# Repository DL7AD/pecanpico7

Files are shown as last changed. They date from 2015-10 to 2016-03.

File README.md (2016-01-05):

# Pecan Pico 7 Balloon Tracker

Pecan Pico 7 is an APRS & SSDV Tracker based on the STM32F429 microcontroller. Please note that this PCB is untested.

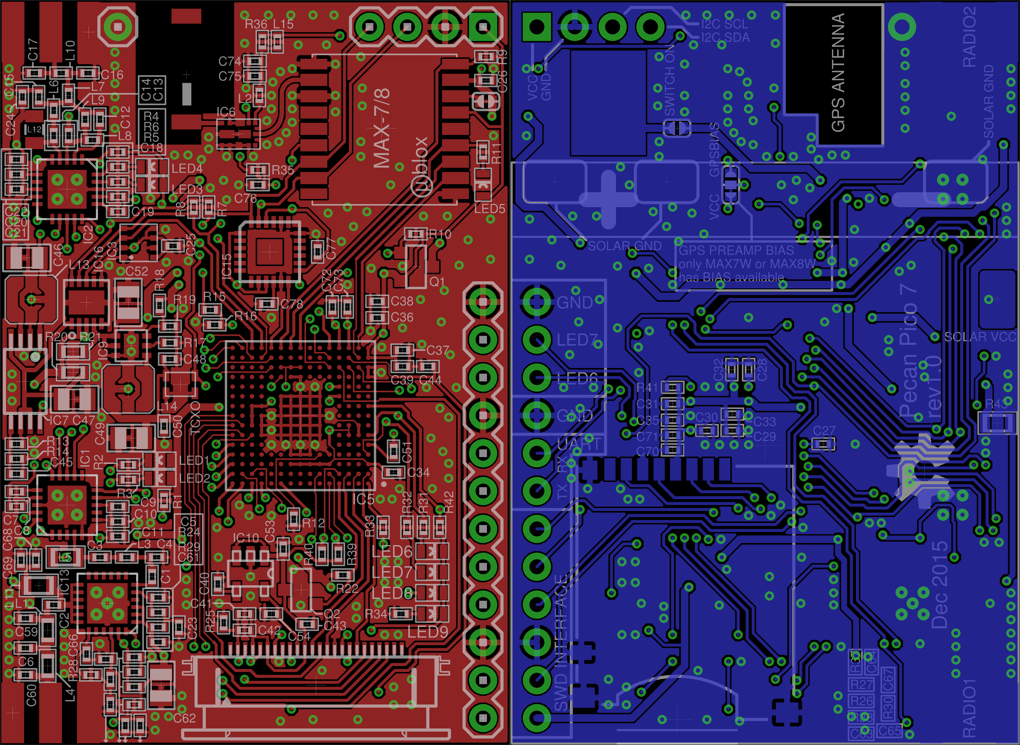
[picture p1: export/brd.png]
Pecan Pico 7


Components
==========

| Component | Description | Purpose on PCB
| --- | --- | ---
| [**Camera OV9655 option**](https://raw.githubusercontent.com/DL7AD/pecanpico7/master/export/sch_camera.png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)
| TI TC1185-1.8VCT713 | LDO | Generate camera core voltage
| OmniVision OV9655 | Camera | Taking pictures
| [**Camera OV2640 option**](https://raw.githubusercontent.com/DL7AD/pecanpico7/master/export/sch_camera.png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)
| TI LP5951MF-1.3/NOPB | LDO | Generate camera core voltage
| OmniVision OV2640 | Camera | Taking pictures
| [**Clock**](https://raw.githubusercontent.com/DL7AD/pecanpico7/master/export/sch_clock.png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)
| Epson TG-5006CJ-19H | TCXO 26MHz | Generate clock for STM32 and transceivers
| [**GNSS**](https://raw.githubusercontent.com/DL7AD/pecanpico7/master/export/sch_gps.png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)
| ublox MAX-7C | GNSS receiver | Receive GPS or GLONASS
| Avago ALM-GP003 | Preamplifier | Filters and preamplifies GNSS signal
| [**IO**](https://raw.githubusercontent.com/DL7AD/pecanpico7/master/export/sch_io.png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)
| *not specified* | microSD card | Flash memory (take any microSD card whatever you want)
| [**Micro Processor Unit (MPU)**](https://raw.githubusercontent.com/DL7AD/pecanpico7/master/export/sch_mpu.png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)
| STM32F429IIH6 | MCU | Controlling all actions on the PCB
| [**Power management**](https://raw.githubusercontent.com/DL7AD/pecanpico7/master/export/sch_power_management.png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)
| ST SPV1040 | Solar battery charger  | Charging the battery from solar cells
| TI TPS62260DRVT | Step-Down regulator | Step down voltage from battery to Vcc rail (2.5V)
| Microchip PAC1720-1-AIA-TR | Current/Voltage sensor | Measure battery input and output current and battery voltage
| [**Radios**](https://raw.githubusercontent.com/DL7AD/pecanpico7/master/export/sch_radios.png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)
| SiLabs Si4060 (Radio 1) | Transmitter (2m) | Transmitting on 2m with 3W
| rfmd RF6886 | Power amplifier | Amplify singal from Radio 1
| SiLabs Si4464 (Radio 2) | Transceiver (70cm) | Transmit and Receive on 70cm with 10mW
| [**Sensing**](https://raw.githubusercontent.com/DL7AD/pecanpico7/master/export/sch_sensing.png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)
| Bosch BME280 | Airpressure sensor | Measuring airpressure, humidity, temperature
| Invensense MPU-9250 | Power amplifier | Measure acceleration, rotation, Earth's magnetic field

Bus connections to peripheral devices
=====================================

There are two I2C bus and one SPI and two UART buses available on the the PCB.
The SPI bus is dedicated to the SiLabs radios. One UART is connected to the GNSS
receiver while the other is available for external debugging purposes. There are
two additional I2C buses. One is used for the camera while the other is used for
everything else. This has been done to avoid routing the I2C through dense
regions on the PCB. The second bus of the I2C can be accessed by a pin header
for external peripheral devices such as an external BME280 to measure balloon
pressure.

**I2C**

| Bus | SCL  | SDA
| --- | ---- | ----
| 1 | PB8  | PB9
| 2 | PB10 | PB11

| Component | Bus | Address
| --- | --- | ---
| OmniVision OV9655/OV2640 | 1 | 0x30
| ublox MAX-7C | 2 | 0x42
| Microchip PAC1720-1-AIA-TR  | 2 | 0x4C
| Bosch BME280 | 2 | 0x77
| Invensense MPU-9250 | 2 | 0x69
| External pin header | 2 | -

**SPI**

- SPI SCK: PB13
- SPI MISO: PB14
- SPI MOSI: PB15

| Component | CS at STM32
| --- | ---
| SiLabs Si4060 (Radio 1) | PA11
| SiLabs Si4464 (Radio 2) | PB0

**UART**

| Component | STM32 TXD | STM32 RXD
| --- | --- | ---
| uBlox MAX-7C | PA2 | PA3
| External pin header | PA0 | PA1

Power feeding
=============

Since this tracker is designed for solar use, there's a solar charging chip, a
battery (LiPo) and a discharging regulator on it. The SPV1040 will charge the battery
on the back of the PCB. It will charge the battery up to 4.1V. The voltage of the
battery is then steped down to 2.5V by the TPS62260 which is fed by the battery. With
exception of the RF6886 All parts are fed by the 2.5V (Vcc) rail. The RF6886 is
connected directly to VBAT in order to get more power out of it. The PAC1720 is able
to measure the charge and discharge current of the battery.

**! PCB ERROR:** The PAC1720 can't measure the current consumed by RF6886.

The camera needs an addional voltage for the core. This must be 1.3V (OV2640) or 1.8V
(OV9655). Depending on which camera is used, IC10 must be changed (notes in schematic).
IC10 is switched by Q2 (GPS shutdown MOSFET). If the camera is switched off, IC10
does not get power as well.

Components Shutdown
===================

Every component has it's own shutdown capacility. Some components are switched off
by an additional MOSFET because when standard shutdown functions still need some mA.

| Component | Shutdown | Notes
| --- | --- | ---
| Microchip PAC1720-1-AIA-TR | none | Standby current 5.5uA
| Radio 1 | Pull PA12 high |
| Radio 2 | Pull PB12 high |
| rfmd RF6886 | none |
| Bosch BME280 | none | Standby current 0.2uA
| MPU-9250 | none | Idle mode 8uA
| Camera | Pull PE0 high  | Camera SHDN still draws 1mA
| Clock (TCXO) | none | Needed for STM32 all time
| GPS and GPS preAMP | Pull PE7 high  |
| microSD card | none | SD cards have usually good internal shutdown
| STM32 | none |

Camera connection
=================

The camera is connected to the DCMI interface of the STM32F4 which can handle the
data though the microcontroller internally. The camera itself is connected to a FFC
connector on the PCB. The STM32 data pins are connected to

| STM32 Pin | Function
| --- | ---
| PA4 | DCMI_HSYNC
| PA6 | DCMI_PCLK
| PB6 | DCMI_D5
| PB7 | DCMI_VSYNC
| PC6 | DCMI_D0
| PC7 | DCMI_D1
| PC8 | DCMI_D2
| PE4 | DCMI_D3
| PB6 | DCMI_D4
| PE5 | DCMI_D6
| PE6 | DCMI_D7

Known PCB errors
================

**ERROR 1:** RF6886 connected incorrectly to PAC1720 (fixable)<br />
Effect: PAC1720 can't measure the current consumed by RF6886<br />
Solution: *none* (will be fixed on next revision)

**ERROR 2:** Capacitor missing at TPS62260DRVT (fixable)<br />
Effect: This capacitor is responsible to reduce voltage ripple on Vcc rail.<br />
Solution: Solder a capacitor (22pF 0402) on top of R18

**ERROR 3:** BYPASS_REG connected to Vcc (fixable)<br />
Effect: The STM32 doesn't starup because internal voltage regulate is shut down<br />
Solution: Desolder R41 and connect BYPASS_REG to GND (put solder junction to resistor pad next to R41)

**ERROR 4:** Wrong oscillator only supplies 0.7V (fixable)<br />
Effect: The external oscillator can't be used for the STM32<br />
Solution: Use an TXC 7L 26MHz oscillator instead or use the internal oscillator

**WARNING 1:** LEDs connected to transceivers are switched on<br />
Effect: Current draw on startup. It could prevent the PCB to startup when the battery is dischanged completely, when the SPV1040 doesn't provide enough power. So the STM32 doesnt boot.<br />
Solution: *none* (will be fixed on next revision) or desolder LEDs

**WARNING 2:** Pad extremly large on PAC1720 and MPU9250<br />
Effect: It could cause solder junctions in production<br />
Solution: *none* (will be fixed on next revision) or put less solder on the pads

**WARNING 3:** Solder jumper included in soldermask<br />
Effect: *no electrical effect*<br />
Solution: *none* (will be fixed on next revision)

**WARNING 4:** RF6886 draws much current in idle<br />
Effect: *no functional limitation*<br />
Solution: *none* (will be fixed on next revision)

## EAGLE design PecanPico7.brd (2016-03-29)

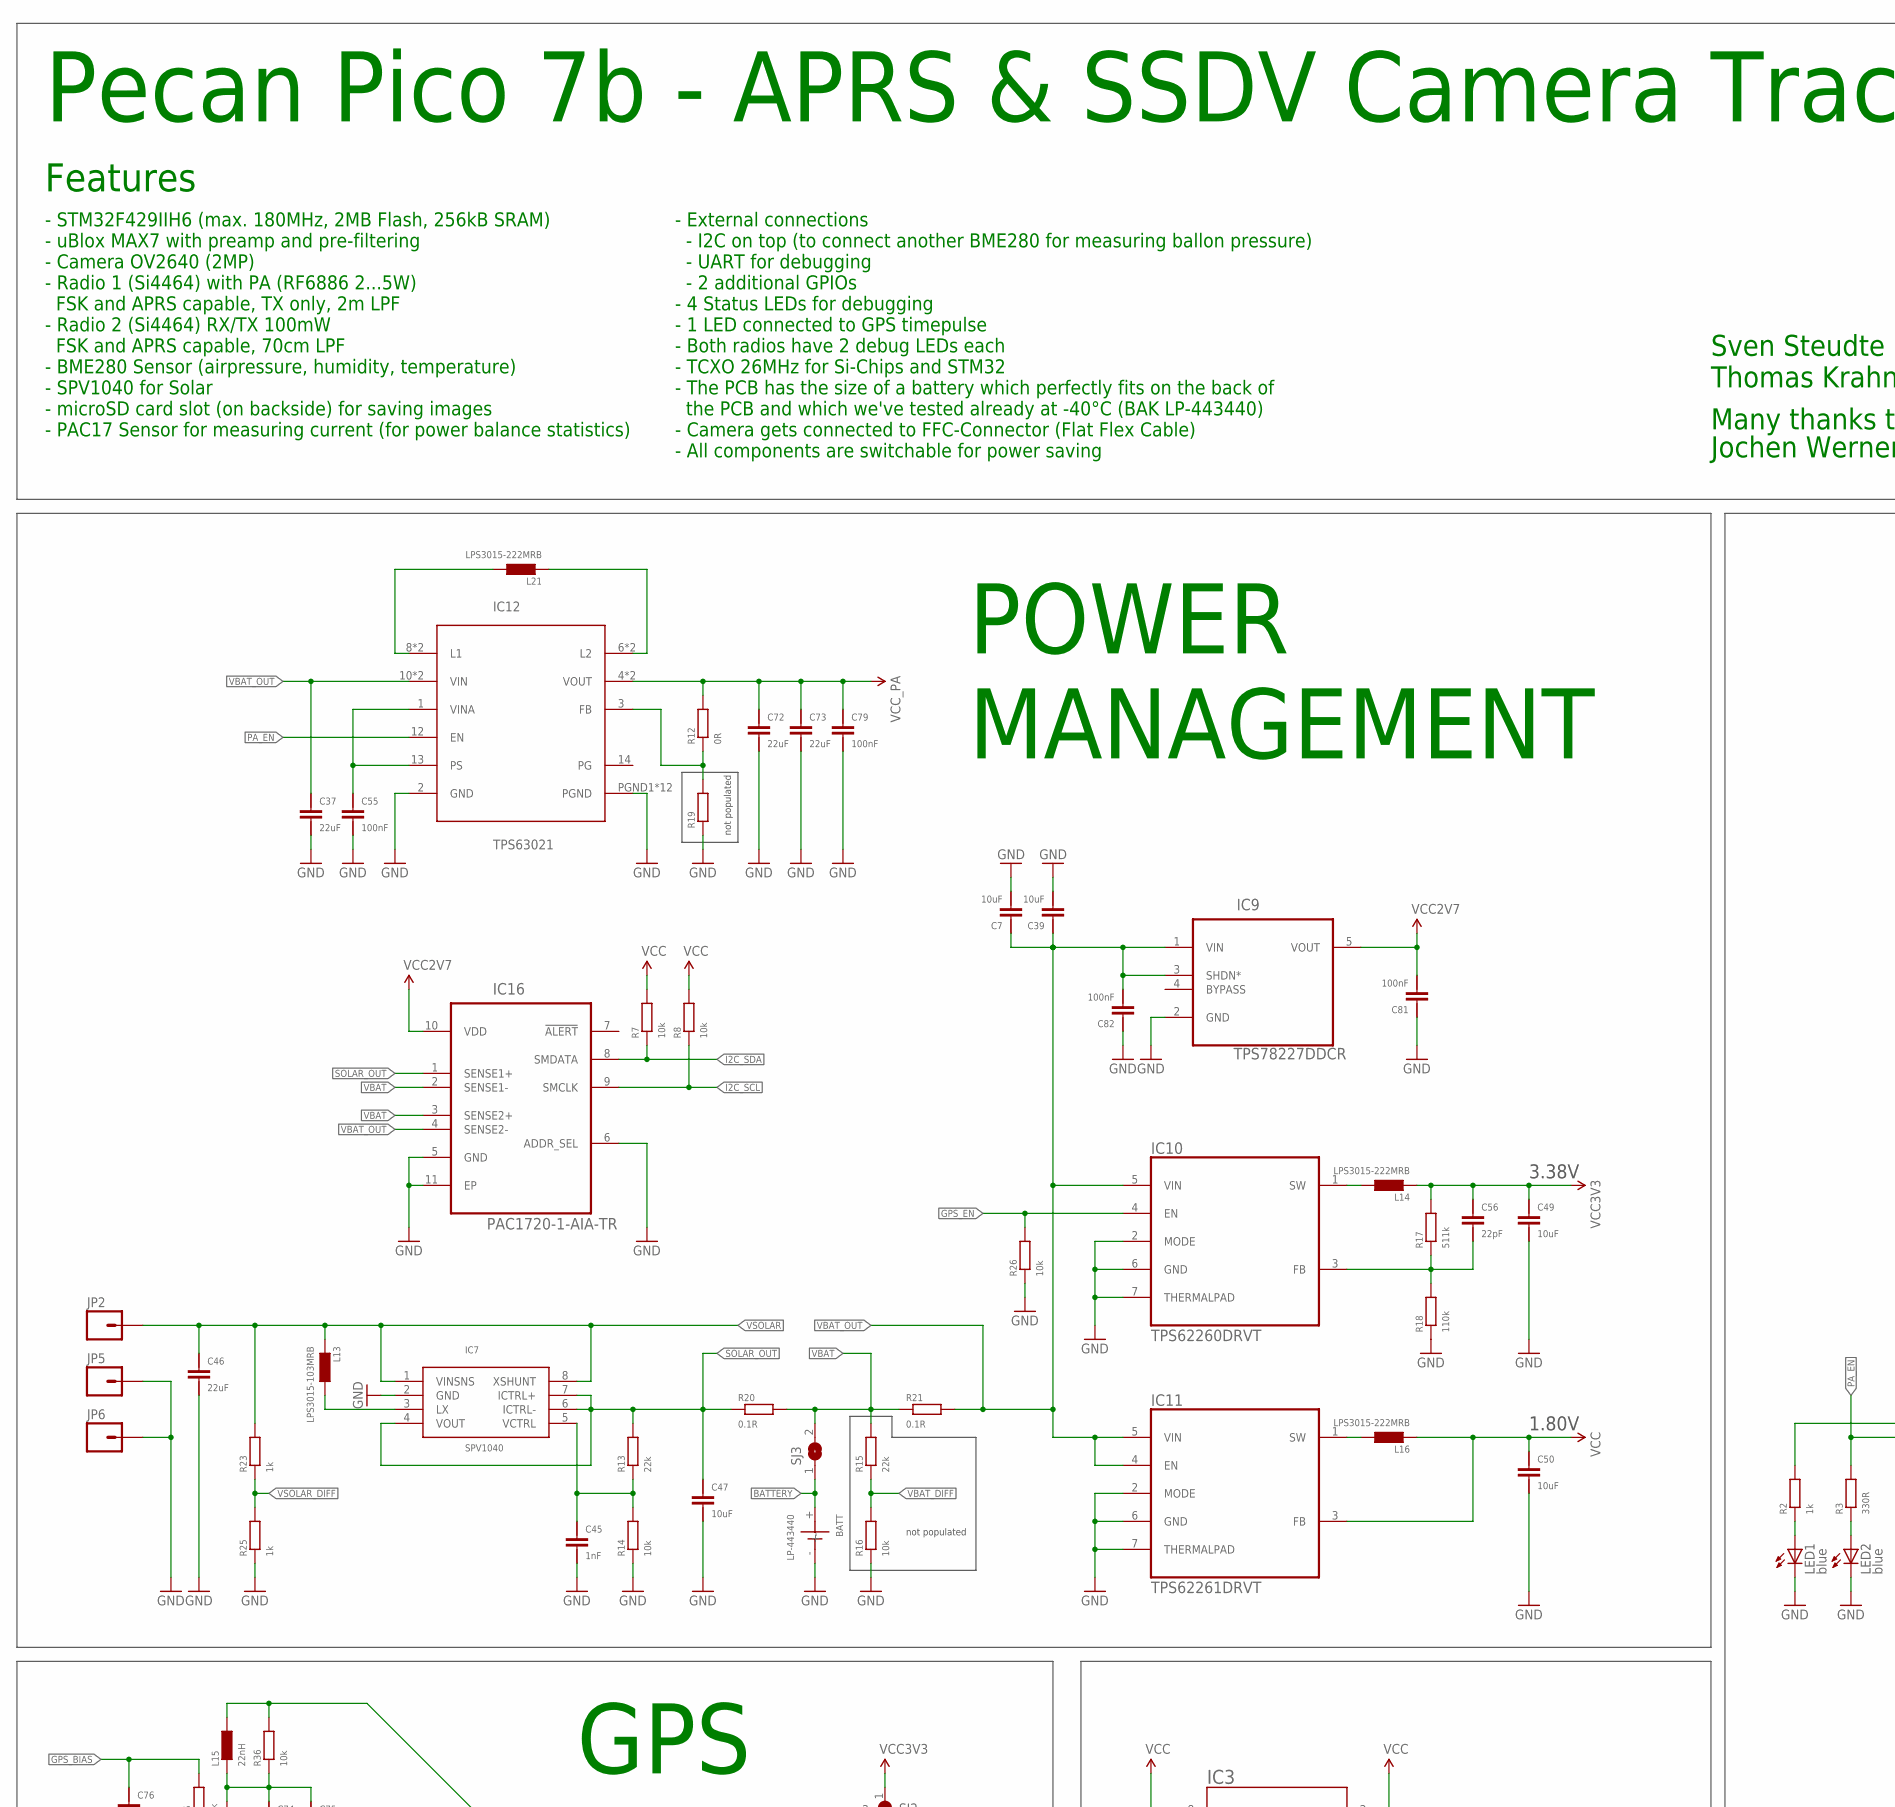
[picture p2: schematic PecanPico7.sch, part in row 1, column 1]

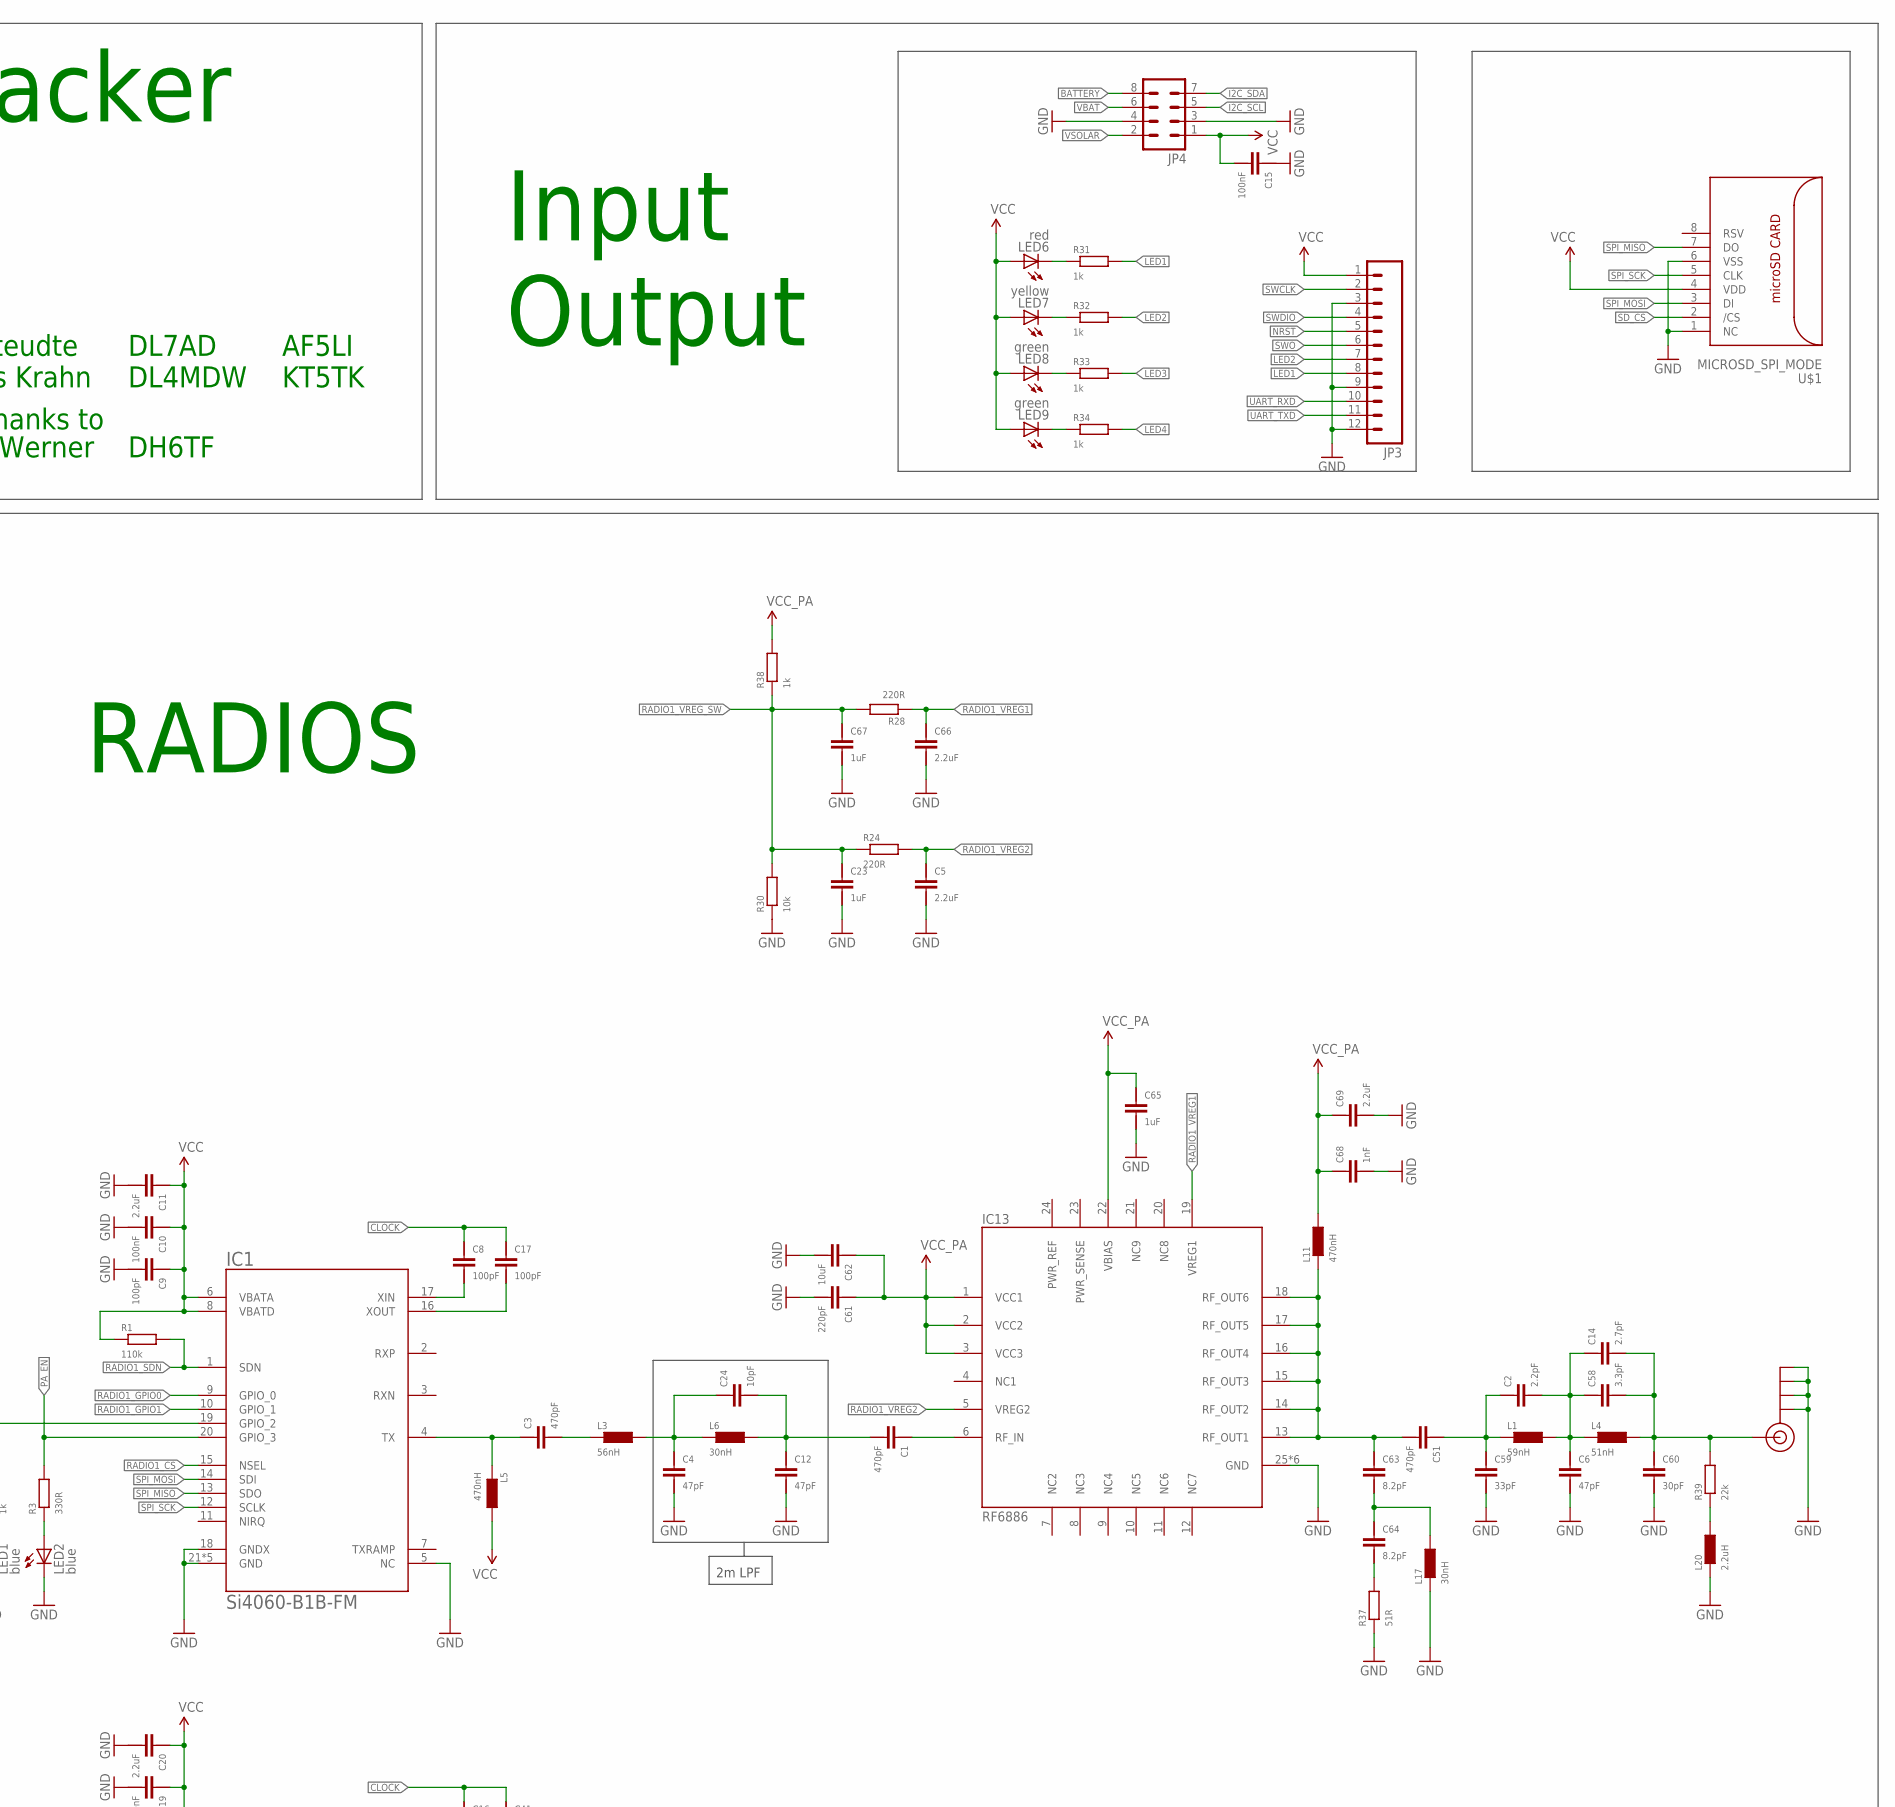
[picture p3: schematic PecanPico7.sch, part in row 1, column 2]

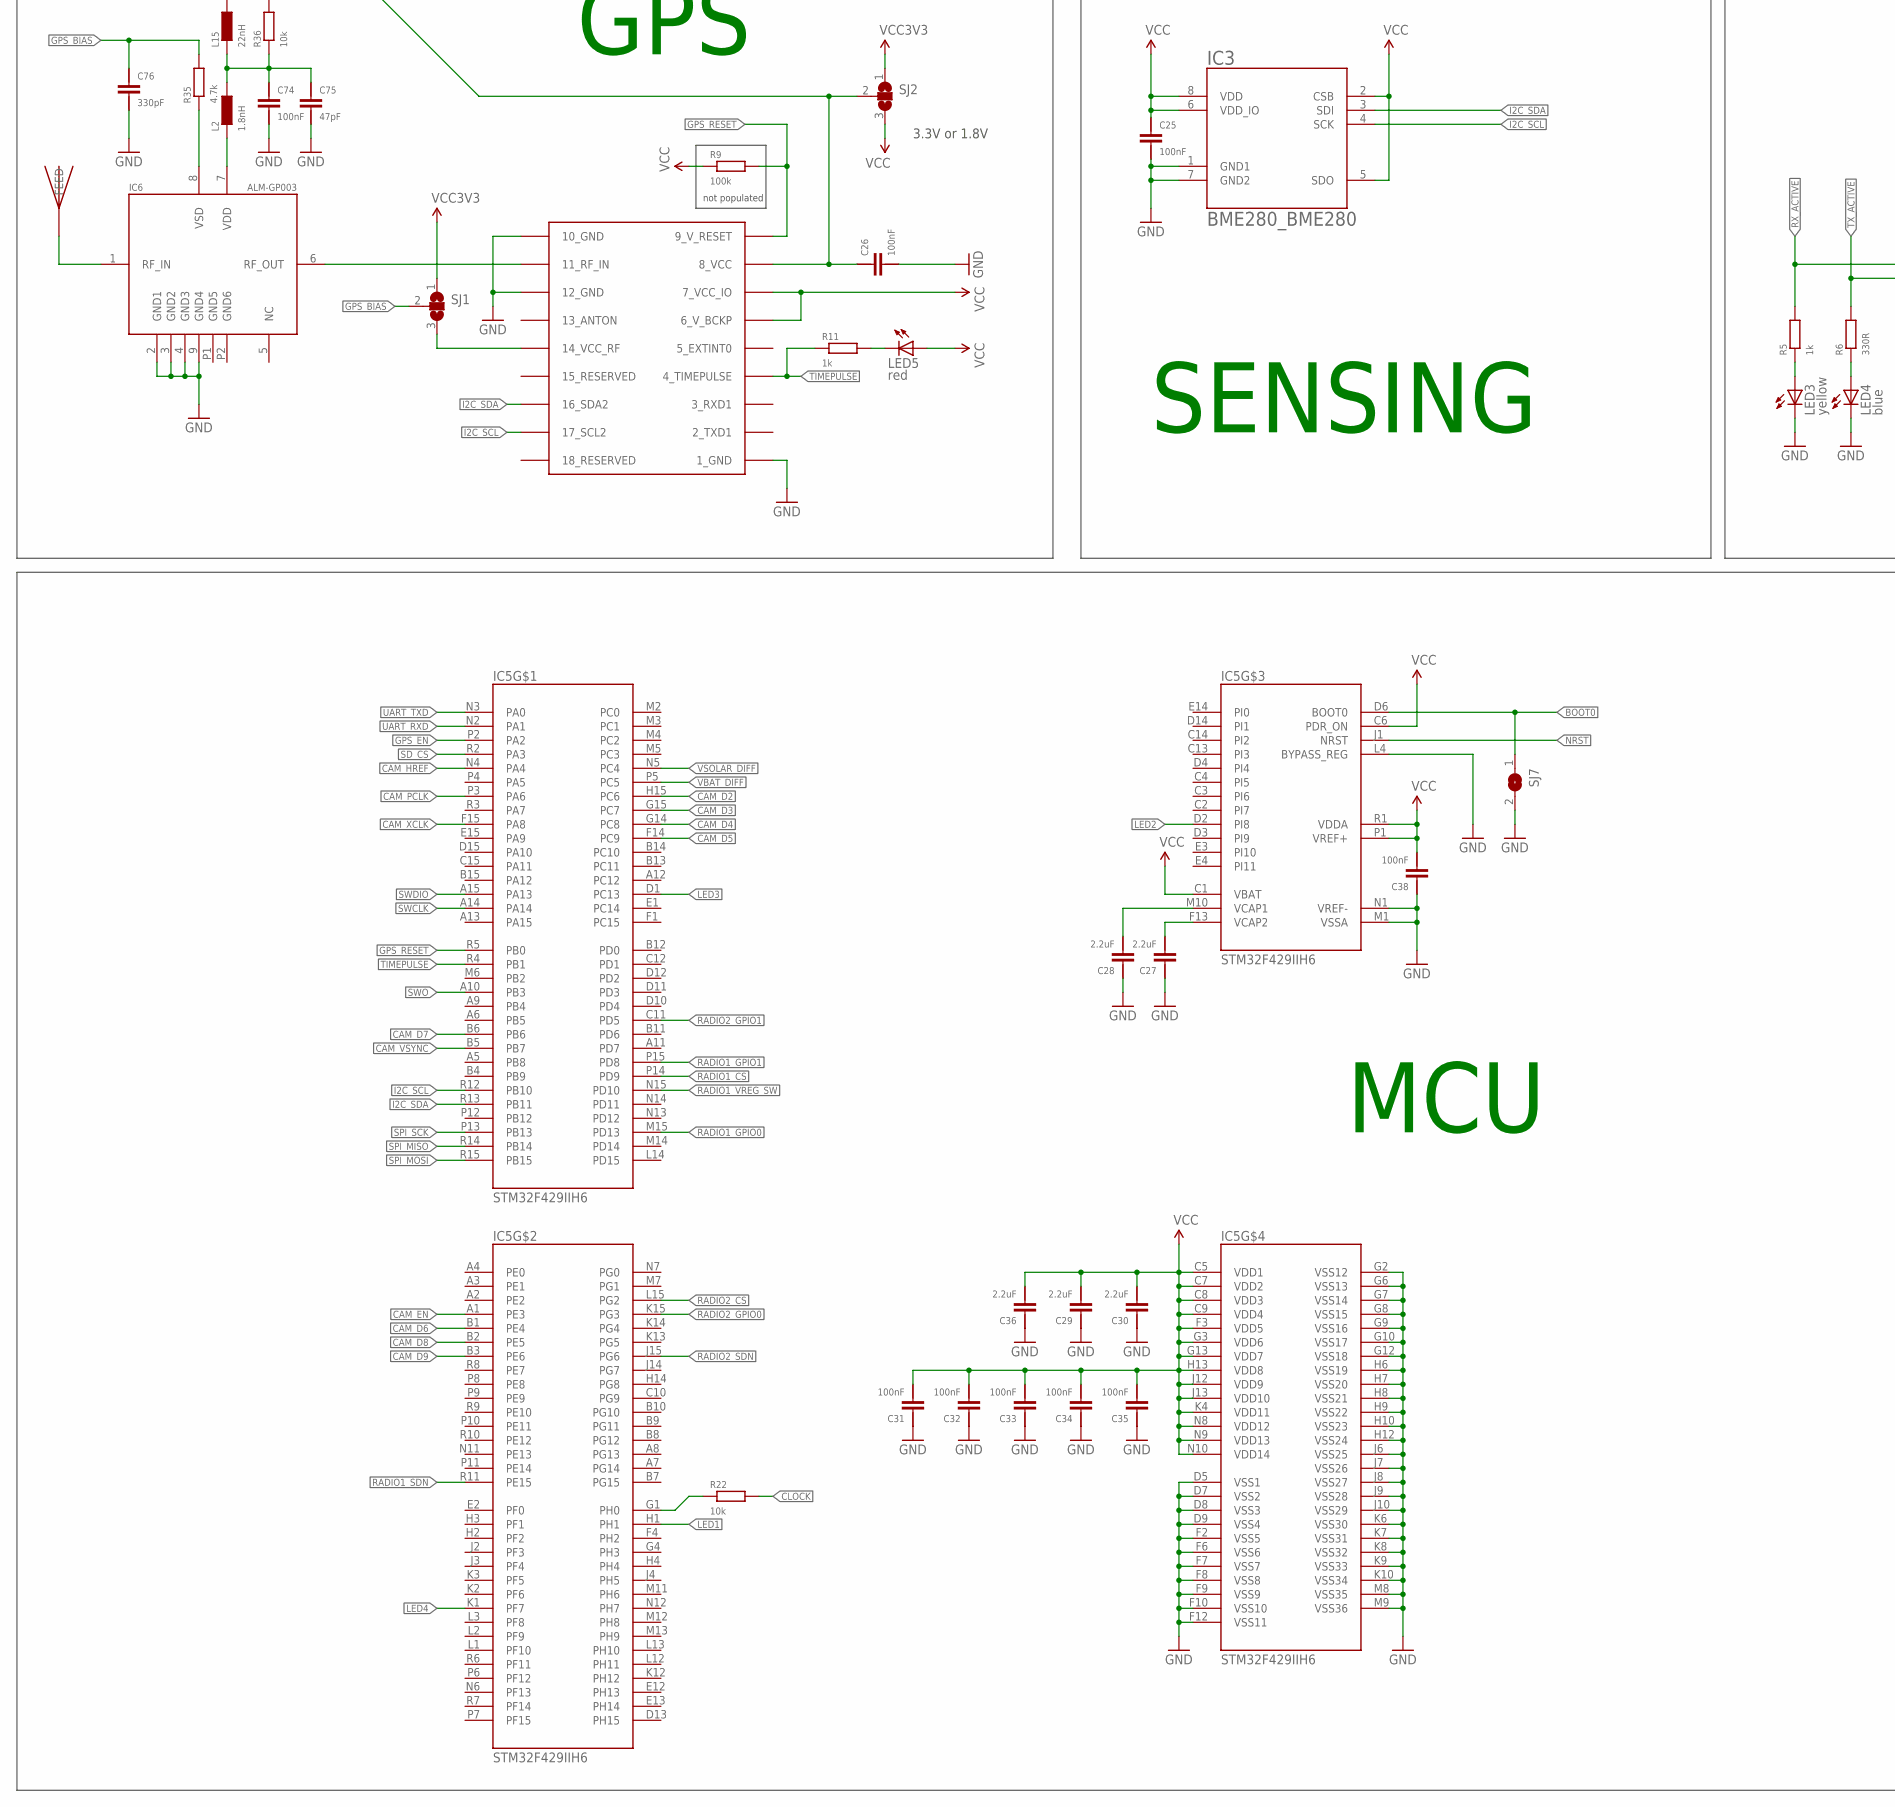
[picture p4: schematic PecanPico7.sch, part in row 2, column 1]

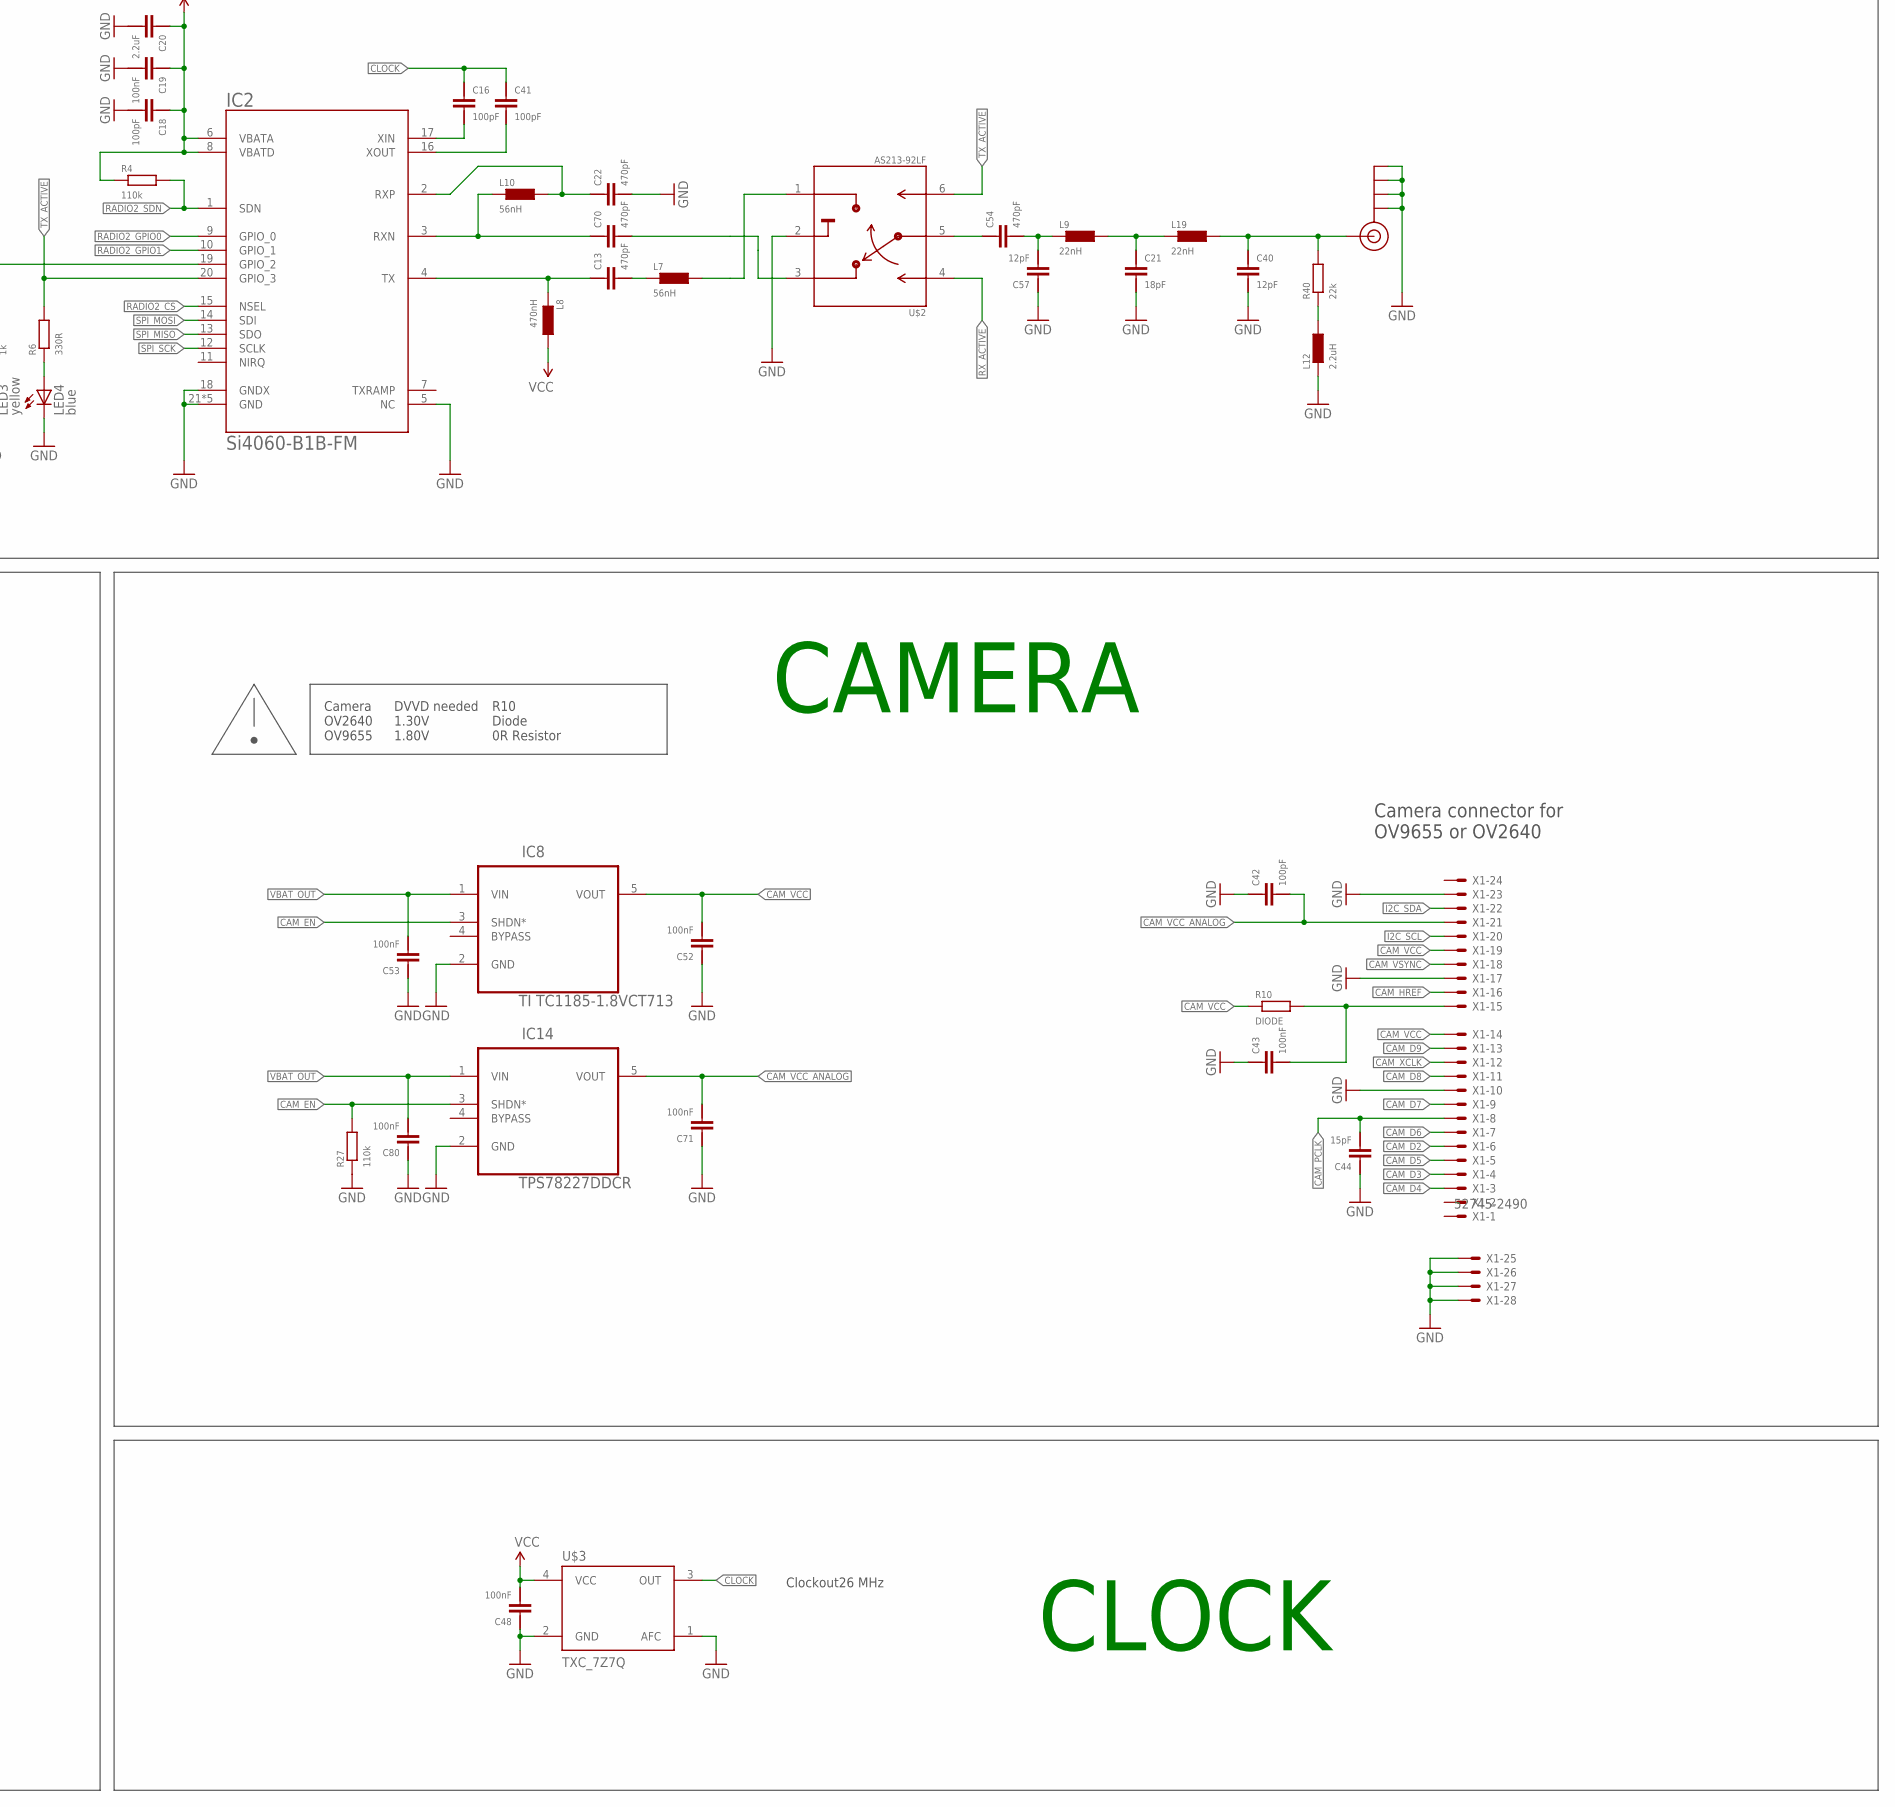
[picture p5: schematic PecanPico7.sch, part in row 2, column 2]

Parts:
BATT: LP-443440
C1, C3, C13, C22, C51, C54, C70: 470pF; 0402
C2: 2.2pF; 0402
C4, C6, C12, C75: 47pF; 0402
C5, C11, C20, C27, C28, C29, C30, C36, C66, C69: 2.2uF; 0402
C7, C39, C47, C49, C50, C62: 10uF; 0805
C8, C9, C16, C17, C18, C41, C42: 100pF; 0402
C10, C15, C19, C25, C26, C31, C32, C33, C34, C35, C38, C43, C48, C52, C53, C55, C71, C74, C79, C80, C81, C82: 100nF; 0402
C14: 2.7pF; 0402
C21: 18pF; 0402
C23, C65, C67: 1uF; 0402
C24: 10pF; 0402
C37, C46, C72, C73: 22uF; 0805
C40, C57: 12pF; 0402
C44: 15pF; 0402
C45, C68: 1nF; 0402
C56: 22pF; 0402
C58: 3.3pF; 0402
C59: 33pF; 0402
C60: 30pF; 0402
C61: 220pF; 0402
C63, C64: 8.2pF; 0402
C76: 330pF; 0402
IC1, IC2: Si4060-B1B-FM; QFN-20
IC3: BME280_BME280
IC4: uBlox MAX7/8; UBLOX_MAX-6
IC5: STM32F429IIH6; UFBGA176
IC6: ALM-GP003
IC7: SPV1040; TSSOP8
IC8: TI TC1185-1.8VCT713; SOT95P290X145-5N
IC9, IC14: TPS78227DDCR; SOT95P290X145-5N
IC10: TPS62260DRVT; SON65P210X210X80-7N
IC11: TPS62261DRVT; SON65P210X210X80-7N
IC12: TPS63021; QFN-14
IC13: RF6886; QFN-24
IC16: PAC1720-1-AIA-TR; DFN300X300X90-11N
J$1, J$2: SMA_EDGE; SMA-EDGE
JP2, JP5, JP6: M01SMD; LUXEON-PAD
JP3: M12PTH; 1X12
JP4: M04X2SMD; 2X4_2
L1: 59nH; 0603@1
L2: 1.8nH; 0402
L3, L7, L10: 56nH; 0402
L4: 51nH; 0603@1
L5, L8, L11: 470nH; 0805@1
L6: 30nH; 0402
L9, L15, L19: 22nH; 0402
L12, L20: 2.2uH; 0402
L13: LPS3015-103MRB; LPS3015
L14, L16, L21: LPS3015-222MRB; LPS3015
L17: 30nH; 0603@1
LED1, LED2, LED4: blue; LED-0603
LED3, LED7: yellow; LED-0603
LED5, LED6: red; LED-0603
LED8, LED9: green; LED-0603
R1, R4, R18, R27: 110k; 0402
R2, R5, R11, R23, R25, R31, R32, R33, R34, R38: 1k; 0402
R3, R6: 330R; 0402
R7, R8, R14, R16, R22, R26, R30, R36: 10k; 0402
R9: 100k; 0402
R10: DIODE; 0402
R12: 0R; 0402
R13, R15, R39, R40: 22k; 0402
R17: 511k; 0402
R19: RES-0402; 0402
R20, R21: 0.1R; 0603
R24, R28: 220R; 0402
R35: 4.7k; 0402
R37: 51R; 0402
SJ1, SJ2: SJ2W; SJ_2
SJ3, SJ7: SJ
U$1: MICROSD_SPI_MODE; MICRO_SD_CONNECTOR
U$2: AS213-92LF; SC-70
U$3: TXC_7Z7Q; TCXO_3.2X2.5
U$4: JTI_ANTENNA-1575AT43A40
X1: 52745-2490

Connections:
BATTERY: BATT.+, JP4.8, SJ3.1
BOOT0: IC5.D6 (BOOT0), SJ7.1
CAM_D2: IC5.H15 (PC6), X1.6
CAM_D3: IC5.G15 (PC7), X1.4
CAM_D4: IC5.G14 (PC8), X1.3
CAM_D5: IC5.F14 (PC9), X1.5
CAM_D6: IC5.B1 (PE4), X1.7
CAM_D7: IC5.B6, X1.9
CAM_D8: IC5.B2 (PE5), X1.11
CAM_D9: IC5.B3 (PE6), X1.13
CAM_EN: IC5.A1 (PE3), IC8.3 (SHDN*), IC14.3 (SHDN*), R27.P$2 (2)
CAM_HREF: IC5.N4 (PA4), X1.16
CAM_PCLK: C44.P$1 (1), IC5.P3 (PA6), X1.8
CAM_VCC: C52.P$1 (1), IC8.5 (VOUT), R10.P$1 (1), X1.14, X1.19
CAM_VCC_ANALOG: C42.P$1 (1), C71.P$1 (1), IC14.5 (VOUT), X1.21
CAM_VSYNC: IC5.B5 (PB7), X1.18
CAM_XCLK: IC5.F15 (PA8), X1.12
CLOCK: C8.P$2 (2), C16.P$2 (2), C17.P$2 (2), C41.P$2 (2), R22.P$2 (2), U$3.3 (OUT)
GND: BATT.-, C4.P$1 (1), C5.P$1 (1), C6.P$1 (1), C7.1, C9.P$1 (1), C10.P$1 (1), C11.P$1 (1), C12.P$1 (1), C15.P$2 (2), C18.P$1 (1), C19.P$1 (1), C20.P$1 (1), C21.P$1 (1), C22.P$1 (1), C23.P$1 (1), C25.P$1 (1), C26.P$1 (1), C27.P$2 (2), C28.P$2 (2), C29.P$2 (2), C30.P$2 (2), C31.P$2 (2), C32.P$2 (2), C33.P$2 (2), C34.P$2 (2), C35.P$2 (2), C36.P$2 (2), C37.1, C38.P$2 (2), C39.1, C40.P$1 (1), C42.P$2 (2), C43.P$2 (2), C44.P$2 (2), C45.P$1 (1), C46.1, C47.1, C48.P$2 (2), C49.1, C50.1, C52.P$2 (2), C53.P$2 (2), C55.P$1 (1), C57.P$2 (2), C59.P$1 (1), C60.P$1 (1), C61.P$1 (1), C62.1, C65.P$1 (1), C66.P$1 (1), C67.P$1 (1), C68.P$1 (1), C69.P$1 (1), C71.P$2 (2), C72.1, C73.1, C74.P$1 (1), C75.P$1 (1), C76.P$1 (1), C79.P$1 (1), C80.P$2 (2), C81.P$2 (2), C82.P$2 (2), IC1.5 (NC), IC1.18 (GNDX), IC1.21 (GND), IC1.22 (GND), IC1.23 (GND), IC1.24 (GND), IC1.25 (GND), IC2.5 (NC), IC2.18 (GNDX), IC2.21 (GND), IC2.22 (GND), IC2.23 (GND), IC2.24 (GND), IC2.25 (GND), IC3.1 (GND1), IC3.7 (GND2), IC4.1_GND, IC4.10_GND, IC4.12_GND, IC5.D5 (VSS1), IC5.D7 (VSS2), IC5.D8 (VSS3), IC5.D9 (VSS4), IC5.F2 (VSS5), IC5.F6 (VSS6), IC5.F7 (VSS7), IC5.F8 (VSS8), IC5.F9 (VSS9), IC5.F10 (VSS10), IC5.F12 (VSS11), IC5.G2 (VSS12), IC5.G6 (VSS13), IC5.G7 (VSS14), IC5.G8 (VSS15), IC5.G9 (VSS16), IC5.G10 (VSS17), IC5.G12 (VSS18), IC5.H6 (VSS19), IC5.H7 (VSS20), IC5.H8 (VSS21), IC5.H9 (VSS22), IC5.H10 (VSS23), IC5.H12 (VSS24), IC5.J6 (VSS25), IC5.J7 (VSS26), IC5.J8 (VSS27), IC5.J9 (VSS28), IC5.J10 (VSS29), IC5.K6 (VSS30), IC5.K7 (VSS31), IC5.K8 (VSS32), IC5.K9 (VSS33), IC5.K10 (VSS34), IC5.L4 (BYPASS_REG), IC5.M1 (VSSA), IC5.M8 (VSS35), IC5.M9 (VSS36), IC5.N1 (VREF-), IC6.2 (GND1), IC6.3 (GND2), IC6.4 (GND3), IC6.9 (GND4), IC7.2 (GND), IC8.2 (GND), IC9.2 (GND), IC10.2 (MODE), IC10.6 (GND), IC10.7 (THERMALPAD), IC11.2 (MODE), IC11.6 (GND), IC11.7 (THERMALPAD), IC12.2 (GND), IC12.PGND1 (PGND), IC12.PGND2 (PGND), IC12.PGND3 (PGND), IC12.PGND4 (PGND), IC12.PGND5 (PGND), IC12.PGND6 (PGND), IC12.PGND7 (PGND), IC12.PGND8 (PGND), IC12.PGND9 (PGND), IC12.PGND10 (PGND), IC12.PGND11 (PGND), IC12.PGND12 (PGND), IC13.25 (GND), IC13.GND, IC13.P$26 (GND), IC13.P$27 (GND), IC13.P$28 (GND), IC13.P$29 (GND), IC14.2 (GND), IC16.5 (GND), IC16.6 (ADDR_SEL), IC16.11 (EP), J$1.GND@0 (GND), J$1.GND@1 (GND), J$1.GND@2 (GND), J$1.GND@3 (GND), J$2.GND@0 (GND), J$2.GND@1 (GND), J$2.GND@2 (GND), J$2.GND@3 (GND), JP3.3, JP3.9, JP3.12, JP4.3, JP4.4, JP5.P$1, JP6.P$1, L12.P$1 (1), L17.P$1 (1), L20.P$1 (1), LED1.C, LED2.C, LED3.C, LED4.C, R14.P$1 (1), R16.P$1 (1), R18.P$1 (1), R19.P$1 (1), R25.P$1 (1), R26.P$1 (1), R27.P$1 (1), R30.P$1 (1), R37.P$1 (1), SJ7.2, U$1.1 (NC), U$1.6 (VSS), U$2.2 (GND), U$3.1 (AFC), U$3.2 (GND), X1.10, X1.17, X1.23, X1.P$1, X1.P$2, X1.P$3, X1.P$4
GPS_BIAS: C76.P$2 (2), R35.P$2 (2), SJ1.2
GPS_EN: IC5.P2 (PA2), IC10.4 (EN), R26.P$2 (2)
GPS_RESET: IC4.9_V_RESET, IC5.R5 (PB0), R9.P$2 (2)
I2C_SCL: IC3.4 (SCK), IC4.17_SCL2, IC5.R12 (PB10), IC16.9 (SMCLK), JP4.5, R8.P$1 (1), X1.20
I2C_SDA: IC3.3 (SDI), IC4.16_SDA2, IC5.R13 (PB11), IC16.8 (SMDATA), JP4.7, R7.P$1 (1), X1.22
LED1: IC5.H1, JP3.8, R31.P$2 (2)
LED2: IC5.D2 (PI8), JP3.7, R32.P$2 (2)
LED3: IC5.D1 (PC13), R33.P$2 (2)
LED4: IC5.K1 (PF7), R34.P$2 (2)
unnamed: C4.P$2 (2), C24.P$2 (2), L3.P$2 (2), L6.P$1 (1)
unnamed: C3.P$2 (2), IC1.4 (TX), L5.P$1 (1)
unnamed: C3.P$1 (1), L3.P$1 (1)
unnamed: C70.P$2 (2), IC2.3 (RXN), L10.P$1 (1)
unnamed: C2.P$1 (1), C6.P$2 (2), C14.P$2 (2), C58.P$2 (2), L1.P$2 (2), L4.P$1 (1)
unnamed: C1.P$2 (2), IC13.6 (RF_IN)
unnamed: IC6.1 (RF_IN), U$4.FEED
unnamed: C2.P$2 (2), C51.P$2 (2), C59.P$2 (2), L1.P$1 (1)
unnamed: C17.P$1 (1), IC1.16 (XOUT)
unnamed: C1.P$1 (1), C12.P$2 (2), C24.P$1 (1), L6.P$2 (2)
unnamed: L7.P$2 (2), U$2.1 (B2)
unnamed: C43.P$1 (1), R10.P$2 (2), X1.15
unnamed: IC1.19 (GPIO_2), R2.P$2 (2)
unnamed: C13.P$2 (2), IC2.4 (TX), L8.P$1 (1)
unnamed: C13.P$1 (1), L7.P$1 (1)
unnamed: C63.P$1 (1), C64.P$2 (2), L17.P$2 (2)
unnamed: C16.P$1 (1), IC2.17 (XIN)
unnamed: C41.P$1 (1), IC2.16 (XOUT)
unnamed: LED3.A, R5.P$1 (1)
unnamed: LED1.A, R2.P$1 (1)
unnamed: LED2.A, R3.P$1 (1)
unnamed: LED4.A, R6.P$1 (1)
unnamed: C64.P$1 (1), R37.P$2 (2)
unnamed: C21.P$2 (2), L9.P$2 (2), L19.P$1 (1)
unnamed: C70.P$1 (1), U$2.3 (B1)
unnamed: LED5.C, R11.P$2 (2)
unnamed: C56.P$1 (1), IC10.3 (FB), R17.P$1 (1), R18.P$2 (2)
unnamed: C40.P$2 (2), J$2.SIG (SIGNAL), L19.P$2 (2), R40.P$2 (2)
unnamed: IC10.1 (SW), L14.2_1 (2), L14.2_2 (2), L14.2_3 (2), L14.2_4 (2), L14.2_5 (2), L14.2_6 (2), L14.2_7 (2), L14.2_8 (2), L14.2_9 (2)
unnamed: IC11.1 (SW), L16.2_1 (2), L16.2_2 (2), L16.2_3 (2), L16.2_4 (2), L16.2_5 (2), L16.2_6 (2), L16.2_7 (2), L16.2_8 (2), L16.2_9 (2)
unnamed: C45.P$2 (2), IC7.5 (VCTRL), R13.P$1 (1), R14.P$2 (2)
unnamed: IC4.11_RF_IN, IC6.6 (RF_OUT)
unnamed: C27.P$1 (1), IC5.F13 (VCAP2)
unnamed: C28.P$1 (1), IC5.M10 (VCAP1)
unnamed: C8.P$1 (1), IC1.17 (XIN)
unnamed: IC7.3 (LX), L13.2_1 (2), L13.2_2 (2), L13.2_3 (2), L13.2_4 (2), L13.2_5 (2), L13.2_6 (2), L13.2_7 (2), L13.2_8 (2), L13.2_9 (2)
unnamed: IC5.G1 (PH0), R22.P$1 (1)
unnamed: C26.P$2 (2), IC4.8_VCC, L15.P$2 (2), R36.P$2 (2), SJ2.2
unnamed: C14.P$1 (1), C58.P$1 (1), C60.P$2 (2), J$1.SIG (SIGNAL), L4.P$2 (2), R39.P$2 (2)
unnamed: LED7.C, R32.P$1 (1)
unnamed: C51.P$1 (1), C63.P$2 (2), IC13.13 (RF_OUT1), IC13.14 (RF_OUT2), IC13.15 (RF_OUT3), IC13.16 (RF_OUT4), IC13.17 (RF_OUT5), IC13.18 (RF_OUT6), L11.P$1 (1)
unnamed: IC12.8 (L1), IC12.9 (L1), L21.2_1 (2), L21.2_2 (2), L21.2_3 (2), L21.2_4 (2), L21.2_5 (2), L21.2_6 (2), L21.2_7 (2), L21.2_8 (2), L21.2_9 (2)
unnamed: IC6.8 (VSD), R35.P$1 (1)
unnamed: IC6.7 (VDD), L2.P$1 (1)
unnamed: LED8.C, R33.P$1 (1)
unnamed: LED9.C, R34.P$1 (1)
unnamed: LED6.C, R31.P$1 (1)
unnamed: IC12.6 (L2), IC12.7 (L2), L21.1_1 (1), L21.1_2 (1), L21.1_3 (1), L21.1_4 (1), L21.1_5 (1), L21.1_6 (1), L21.1_7 (1), L21.1_8 (1), L21.1_9 (1)
unnamed: C74.P$2 (2), C75.P$2 (2), L2.P$2 (2), L15.P$1 (1), R36.P$1 (1)
unnamed: IC4.14_VCC_RF, SJ1.3
unnamed: C22.P$2 (2), IC2.2 (RXP), L10.P$2 (2)
unnamed: L20.P$2 (2), R39.P$1 (1)
unnamed: C54.P$2 (2), U$2.5 (A1)
unnamed: C54.P$1 (1), C57.P$1 (1), L9.P$1 (1)
unnamed: L12.P$2 (2), R40.P$1 (1)
unnamed: IC12.3 (FB), R12.P$1 (1), R19.P$2 (2)
unnamed: C55.P$2 (2), IC12.1 (VINA), IC12.13 (PS)
NRST: IC5.J1 (NRST), JP3.5
PA_EN: IC1.20 (GPIO_3), IC12.12 (EN), R3.P$2 (2)
RADIO1_CS: IC1.15 (NSEL), IC5.P14 (PD9)
RADIO1_GPIO0: IC1.9 (GPIO_0), IC5.M15 (PD13)
RADIO1_GPIO1: IC1.10 (GPIO_1), IC5.P15 (PD8)
RADIO1_SDN: IC1.1 (SDN), IC5.R11 (PE15), R1.P$2 (2)
RADIO1_VREG1: C66.P$2 (2), IC13.19 (VREG1), R28.P$1 (1)
RADIO1_VREG2: C5.P$2 (2), IC13.5 (VREG2), R24.P$2 (2)
RADIO1_VREG_SW: C23.P$2 (2), C67.P$2 (2), IC5.N15 (PD10), R24.P$1 (1), R28.P$2 (2), R30.P$2 (2), R38.P$1 (1)
RADIO2_CS: IC2.15 (NSEL), IC5.L15 (PG2)
RADIO2_GPIO0: IC2.9 (GPIO_0), IC5.K15 (PG3)
RADIO2_GPIO1: IC2.10 (GPIO_1), IC5.C11 (PD5)
RADIO2_SDN: IC2.1 (SDN), IC5.J15 (PG6), R4.P$2 (2)
RX_ACTIVE: IC2.19 (GPIO_2), R5.P$2 (2), U$2.4 (V2)
SD_CS: IC5.R2 (PA3), U$1.2 (/CS)
SOLAR_OUT: C47.2, IC7.4 (VOUT), IC7.6 (ICTRL-), IC7.7 (ICTRL+), IC16.1 (SENSE1+), R13.P$2 (2), R20.P$1 (1)
SPI_MISO: IC1.13 (SDO), IC2.13 (SDO), IC5.R14 (PB14), U$1.7 (DO)
SPI_MOSI: IC1.14 (SDI), IC2.14 (SDI), IC5.R15 (PB15), U$1.3 (DI)
SPI_SCK: IC1.12 (SCLK), IC2.12 (SCLK), IC5.P13 (PB13), U$1.5 (CLK)
SWCLK: IC5.A14, JP3.2
SWDIO: IC5.A15 (PA13), JP3.4
SWO: IC5.A10 (PB3), JP3.6
TIMEPULSE: IC4.4_TIMEPULSE, IC5.R4 (PB1), R11.P$1 (1)
TX_ACTIVE: IC2.20 (GPIO_3), R6.P$2 (2), U$2.6 (V1)
UART_RXD: IC5.N2 (PA1), JP3.10
UART_TXD: IC5.N3 (PA0), JP3.11
VBAT: IC16.2 (SENSE1-), IC16.3 (SENSE2+), JP4.6, R15.P$2 (2), R20.P$2 (2), R21.P$1 (1), SJ3.2
VBAT_DIFF: IC5.P5 (PC5), R15.P$1 (1), R16.P$2 (2)
VBAT_OUT: C7.2, C37.2, C39.2, C53.P$1 (1), C80.P$1 (1), C82.P$1 (1), IC8.1 (VIN), IC9.1 (VIN), IC9.3 (SHDN*), IC10.5 (VIN), IC11.4 (EN), IC11.5 (VIN), IC12.10 (VIN), IC12.11 (VIN), IC14.1 (VIN), IC16.4 (SENSE2-), R21.P$2 (2)
VCC: C9.P$2 (2), C10.P$2 (2), C11.P$2 (2), C15.P$1 (1), C18.P$2 (2), C19.P$2 (2), C20.P$2 (2), C25.P$2 (2), C29.P$1 (1), C30.P$1 (1), C31.P$1 (1), C32.P$1 (1), C33.P$1 (1), C34.P$1 (1), C35.P$1 (1), C36.P$1 (1), C38.P$1 (1), C48.P$1 (1), C50.2, IC1.6 (VBATA), IC1.8 (VBATD), IC2.6 (VBATA), IC2.8 (VBATD), IC3.2 (CSB), IC3.5 (SDO), IC3.6 (VDD_IO), IC3.8 (VDD), IC4.6_V_BCKP, IC4.7_VCC_IO, IC5.C1 (VBAT), IC5.C5 (VDD1), IC5.C6 (PDR_ON), IC5.C7 (VDD2), IC5.C8 (VDD3), IC5.C9 (VDD4), IC5.F3 (VDD5), IC5.G3 (VDD6), IC5.G13 (VDD7), IC5.H13 (VDD8), IC5.J12 (VDD9), IC5.J13 (VDD10), IC5.K4 (VDD11), IC5.N8 (VDD12), IC5.N9 (VDD13), IC5.N10 (VDD14), IC5.P1 (VREF+), IC5.R1 (VDDA), IC11.3 (FB), JP3.1, JP4.1, L5.P$2 (2), L8.P$2 (2), L16.1_1 (1), L16.1_2 (1), L16.1_3 (1), L16.1_4 (1), L16.1_5 (1), L16.1_6 (1), L16.1_7 (1), L16.1_8 (1), L16.1_9 (1), LED5.A, LED6.A, LED7.A, LED8.A, LED9.A, R1.P$1 (1), R4.P$1 (1), R7.P$2 (2), R8.P$2 (2), R9.P$1 (1), SJ2.3, U$1.4 (VDD), U$3.4 (VCC)
VCC2V7: C81.P$1 (1), IC9.5 (VOUT), IC16.10 (VDD)
VCC3V3: C49.2, C56.P$2 (2), L14.1_1 (1), L14.1_2 (1), L14.1_3 (1), L14.1_4 (1), L14.1_5 (1), L14.1_6 (1), L14.1_7 (1), L14.1_8 (1), L14.1_9 (1), R17.P$2 (2), SJ1.1, SJ2.1
VCC_PA: C61.P$2 (2), C62.2, C65.P$2 (2), C68.P$2 (2), C69.P$2 (2), C72.2, C73.2, C79.P$2 (2), IC12.4 (VOUT), IC12.5 (VOUT), IC13.1 (VCC1), IC13.2 (VCC2), IC13.3 (VCC3), IC13.22 (VBIAS), L11.P$2 (2), R12.P$2 (2), R38.P$2 (2)
VSOLAR: C46.2, IC7.1 (VINSNS), IC7.8 (XSHUNT), JP2.P$1, JP4.2, L13.1_1 (1), L13.1_2 (1), L13.1_3 (1), L13.1_4 (1), L13.1_5 (1), L13.1_6 (1), L13.1_7 (1), L13.1_8 (1), L13.1_9 (1), R23.P$2 (2)
VSOLAR_DIFF: IC5.N5 (PC4), R23.P$1 (1), R25.P$2 (2)

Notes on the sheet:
CLOCK
CAMERA
RADIOS
POWER MANAGEMENT
GPS
SENSING
MCU
Pecan Pico 7b - APRS & SSDV Camera Tracker
Input Output
Sven Steudte Thomas Krahn
DL7AD DL4MDW
AF5LI KT5TK
- STM32F429IIH6 (max. 180MHz, 2MB Flash, 256kB SRAM) - uBlox MAX7 with preamp and pre-filtering - Camera OV2640 (2MP) - Radio 1 (Si4464) with PA (RF6886 2...5W) FSK and APRS capable, TX only, 2m LPF - Radio 2 (Si4464) RX/TX 100mW FSK and APRS capable, 70cm LPF - BME280 Sensor (airpressure, humidity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
- External connections - I2C on top (to connect another BME280 for measuring ballon pressure) - UART for debugging - 2 additional GPIOs - 4 Status LEDs for debugging - 1 LED connected to GPS timepulse - Both radios have 2 debug LEDs each - TCXO 26MHz for Si-Chips and STM32 - The PCB has the size of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
Features
Camera OV2640 OV9655
DVVD needed 1.30V 1.80V
R10 Diode 0R Resistor
Camera connector for OV9655 or OV2640
Clockout26 MHz
2m LPF
3.3V or 1.8V
1.80V
3.38V
not populated
Many thanks to
Jochen Werner
DH6TF

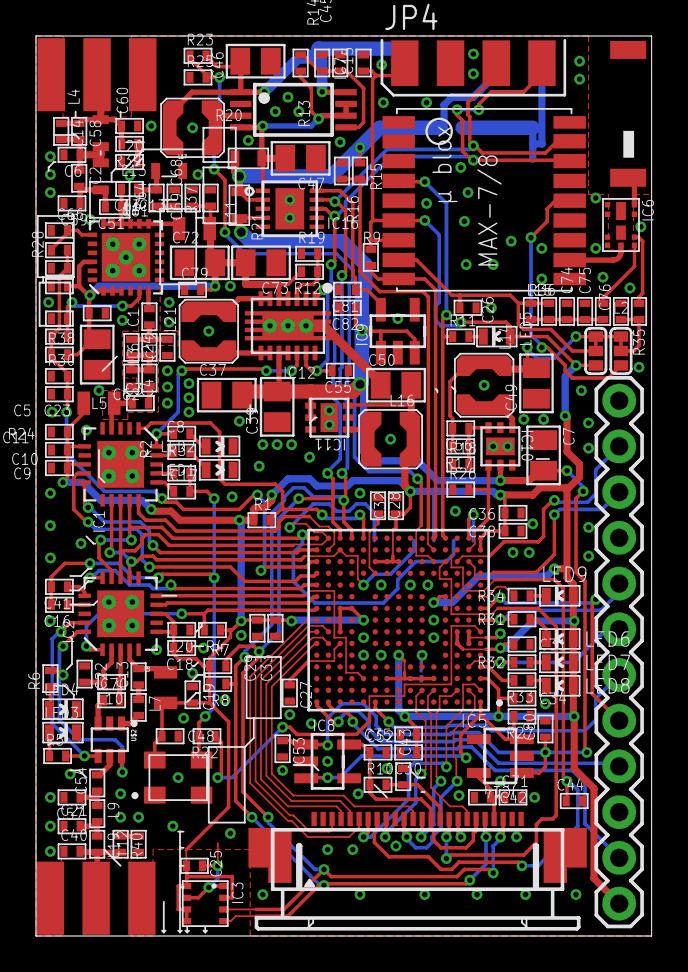
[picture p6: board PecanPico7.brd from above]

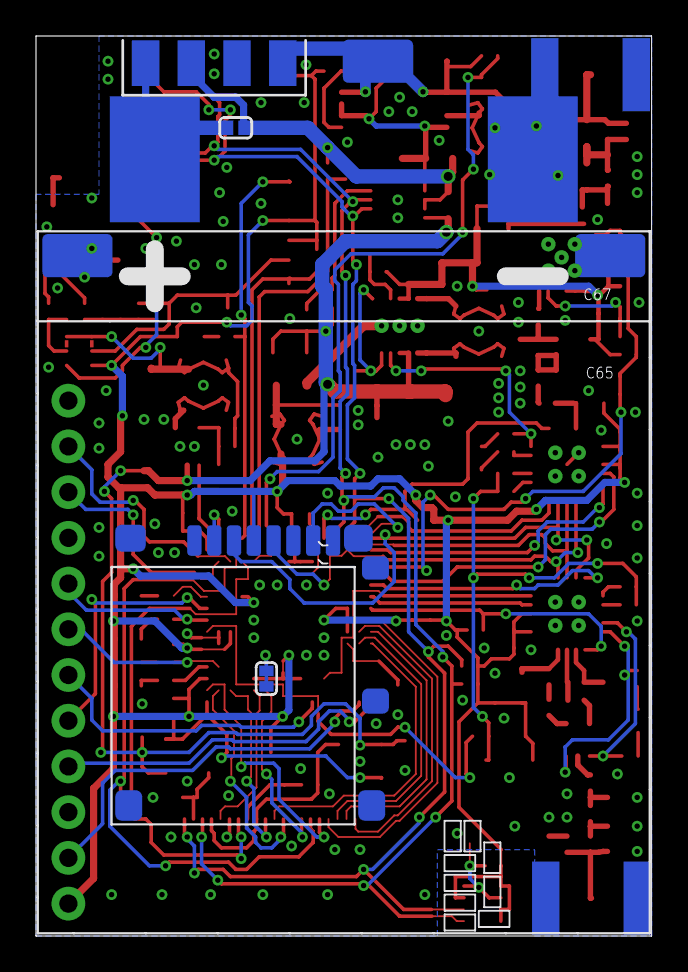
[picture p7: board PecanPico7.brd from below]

Board: 2 copper layers, 34.2 x 50.0 mm, 180 parts (7 on the bottom side), 120 nets.

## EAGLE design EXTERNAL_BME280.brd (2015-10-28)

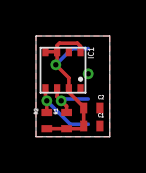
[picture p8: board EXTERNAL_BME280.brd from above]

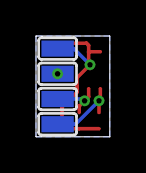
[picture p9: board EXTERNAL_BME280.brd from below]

Board: 2 copper layers, 4.1 x 5.6 mm, 9 parts (4 on the bottom side), 4 nets.

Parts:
C1: 2.2uF; 0402
C2: 100nF; 0402
IC1: BME280
JP1, JP2, JP3, JP4: PAD2_1.8X0.9
R1, R2: 10k; 0402

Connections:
GND: C1.P$1, C2.P$1, IC1.1, IC1.7, JP4.1
unnamed: IC1.3, JP2.1, R1.P$1
unnamed: IC1.4, JP3.1, R2.P$1
VCC: C1.P$2, C2.P$2, IC1.2, IC1.5, IC1.6, IC1.8, JP1.1, R1.P$2, R2.P$2

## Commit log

2015-10-28 Added BME280 breakout board
    [EXTERNAL_BME280.brd, EXTERNAL_BME280.sch]
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2015-10-29 Added Pecan, 2xSi4464, ublox MAX7/8, STM32F427
    [PecanPico7.brd, PecanPico7.sch]
2015-10-29 Renamed external BME280 board
    [ext_BME280.brd, ext_BME280.sch]
2015-10-30 Added SDRAM and routed, Added camera pins
    [PecanPico7.brd, PecanPico7.sch]
2015-10-30 Moved parts around
    [PecanPico7.brd, PecanPico7.sch]
2015-10-30 Moved parts around mainly, changed pinheaders, added busses
    [PecanPico7.brd, PecanPico7.sch]
2015-10-31 Added power management
    [PecanPico7.brd, PecanPico7.sch]
2015-10-31 Reordered power supply components
    [PecanPico7.brd, PecanPico7.sch]
2015-10-31 Moved components around
    [PecanPico7.brd, PecanPico7.sch]
2015-11-01 Fixed all DRC errors
    [PecanPico7.brd]
2015-11-01 Rerouted signals
    [PecanPico7.brd]
2015-11-01 Added LDO's
    [PecanPico7.brd, PecanPico7.sch]
2015-11-19 Done many things Added camera header Removed SDRAM Moved parts around
    [PecanPico7.brd, PecanPico7.sch]
2015-11-20 Added PA for Radio 1 and voltag REF
    [PecanPico7.brd, PecanPico7.sch]
2015-11-20 Resolved DRC errors
    [PecanPico7.brd]
2015-11-21 Added RF6886, moved parts around
    [PecanPico7.brd, PecanPico7.sch]
2015-11-21 Connected ADCs
    [PecanPico7.brd, PecanPico7.sch]
2015-11-21 Connected GPS to STM32F4, moved parts around
    [PecanPico7.brd, PecanPico7.sch]
2015-11-22 Many changes Added REF pullups to PA Added SD card slot Added MOSFET for SD card and camera Added Status LEDS Added capacitors for PA_PWR_REF and PA_PWR_REV Added Debug UART output Added UART to GPS 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
    [PecanPico7.brd, PecanPico7.sch]
2015-11-22 Connected LED pins to pinheader
    [PecanPico7.brd, PecanPico7.sch]
2015-11-23 Added GPS preamplifier
    [PecanPico7.brd, PecanPico7.sch]
2015-11-23 Fixed impedance errors
    [PecanPico7.brd]
2015-11-23 Fixed DRC errors
    [PecanPico7.brd]
2015-11-23 Added MPU9250
    [PecanPico7.brd, PecanPico7.sch]
2015-11-23 Connected GNDs
    [PecanPico7.brd, PecanPico7.sch]
2015-11-24 Fixed errors Fixed wrong connected DCMI pins Fixed missing I2C pull ups Fixed missing voltage dividers at ADC
    [PecanPico7.brd, PecanPico7.sch]
2015-11-26 Fixed errors, moved parts around Fixed GPS BIAS preamp connection Corrected GND polygons Added NRST pullup Added BYPASS_REG pullup Implemented I2C pullups for camera Checked all label connections to 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
    [PecanPico7.brd, PecanPico7.sch]
2015-11-26 Removed SD MOSFET, Added VSOL pad
    [PecanPico7.brd, PecanPico7.sch]
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2015-11-27 Done many things Replaced 0402 sense resistors by 0603 Fixed LPF at Radio 2 Connected Radio 1 PA to VBAT instead of VCC Corrected MPU9250 GND pad Relocated VBAT signal to avoid interference to MPU925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
    [PecanPico7.brd, PecanPico7.sch]
2015-11-27 Added switching SJ to battery
    [PecanPico7.brd, PecanPico7.sch]
2015-11-27 Fixed GPS preamp VCC connection
    [PecanPico7.brd, PecanPico7.sch]
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2015-11-28 Done many things Added solar GND pads Added names to components Done on-board documentation
    [PecanPico7.brd, PecanPico7.sch]
2015-11-29 Fixed camera connection, tidy up
    [PecanPico7.brd, PecanPico7.sch]
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2015-11-29 Fixed text positions
    [PecanPico7.brd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]
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2015-12-03 Fixed incorrect voltage supply at OV2640
    [PecanPico7.brd, PecanPico7.sch]
2015-12-10 Relocated names, added infos, added PCB name
    [PecanPico7.brd, PecanPico7.sch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]
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2015-12-11 Moved Silkscreen, improved GND-connections
    [PecanPico7.brd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]
2015-12-12 Updated sch and brd images
    [ext_BME280.brd, ext_BME280.sch]
2015-12-13 Fixed camera name
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2015-12-27 Adjusted preR of LEDs and voltage divider of TPS62260
    [PecanPico7.brd, PecanPico7.sch]
2015-12-27 Added PCB errors and warnings
2015-12-30 Fixed errors, improved routing Fixed: LED's switched on in sleep Fixed: Solder on solder jumper Fixed: Pad incredible close to each other at SPU9250 and PAC1720 Fixed: BYPASS connected to VCC
    [PecanPico7.brd, PecanPico7.sch]
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2016-01-23 Implemented multiple switching regulators, moved parts around
    [PecanPico7.brd, PecanPico7.sch]
2016-02-09 Moved parts around, removed SD SPI
    [PecanPico7.brd, PecanPico7.sch]
2016-02-09 Moved all components to the top layer
    [PecanPico7.brd, PecanPico7.sch]
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2016-02-10 Added 1.3V LDO for camera
    [PecanPico7.brd, PecanPico7.sch]
2016-02-11 Connected GNDs, inserted LPF to PA VREG
    [PecanPico7.brd, PecanPico7.sch]
2016-02-11 Moved parts around, resolved DRC errors
    [PecanPico7.brd]
2016-02-11 Added micro SD card slot
    [PecanPico7.brd, PecanPico7.sch]
2016-02-11 Removed wires and exposed pad from MPU9250
    [PecanPico7.brd, PecanPico7.sch]
2016-02-12 Moved parts around, changed MCU GPIO connections
    [PecanPico7.brd, PecanPico7.sch]
2016-02-12 Moved camera solder jumper
    [PecanPico7.brd]
2016-02-16 Changed position of radio 1 and 2
    [PecanPico7.brd, PecanPico7.sch]
2016-02-17 Moved parts around, changed values of filters
    [PecanPico7.brd, PecanPico7.sch]
2016-02-18 Changed switching regulators, moved parts around
    [PecanPico7.brd, PecanPico7.sch]
2016-02-18 Removed PA switch MOSFET, moved parts around
    [PecanPico7.brd, PecanPico7.sch]
2016-02-18 Removed DRC errors
    [PecanPico7.brd, PecanPico7.sch]
2016-02-18 Added defaults to solder jumper
    [PecanPico7.brd]
2016-02-23 Added switching regulator for PA
    [PecanPico7.brd, PecanPico7.sch]
2016-02-24 Moved all parts in place
    [PecanPico7.brd, PecanPico7.sch]
2016-03-04 Done many things Changed 2.5V switching regulators to LDOs Connected Si4464 GPIOs and CS Removed GND at LPF Removed MPU9250 Moved parts around
    [PecanPico7.brd, PecanPico7.sch]
2016-03-04 Checked all pins, DRC, adjusted Silkscreen, checked VCC trace width
    [PecanPico7.brd, PecanPico7.sch]
2016-03-04 Adjusted silkscreen, created GERBERs, updated CAM script
    [PecanPico7.brd, PecanPico7.sch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]
2016-03-05 Moved parts around, updated GERBER
    [PecanPico7.brd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]
2016-03-18 Connected TCXO to STM32_OSC pin
    [PecanPico7.brd, PecanPico7.sch]
2016-03-21 Replaced small TCXO package to larger one
    [PecanPico7.brd, PecanPico7.sch]
2016-03-21 Connected radio GPIOs to one UART TX
    [PecanPico7.brd, PecanPico7.sch]
2016-03-22 Modified voltage supply of camera
    [PecanPico7.brd, PecanPico7.sch]
2016-03-22 Added Polygons for MCU
    [PecanPico7.brd]
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2016-03-23 Connected LED4 to MCU pin, added GND cutout
    [PecanPico7.brd, PecanPico7.sch]
2016-03-27 Done many things Added mounting point for camera Replaced 1X4 pin header with 2X4 pinheader (I2C header) Added battery and solar jumper Added voltage divider for Vsolar Removed 100mil mounting point
    [PecanPico7.brd, PecanPico7.sch]
2016-03-28 Moved silkscreen, updated GERBERs
    [PecanPico7.brd, PecanPico7.sch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]
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2016-03-28 Increased size of I2C header
    [PecanPico7.brd, PecanPico7.sch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]
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2016-03-29 Tidy up schematic file
    [PecanPico7.brd, PecanPico7.sch]
2016-03-29 Tidy up schematic file2
    [PecanPico7.sch]

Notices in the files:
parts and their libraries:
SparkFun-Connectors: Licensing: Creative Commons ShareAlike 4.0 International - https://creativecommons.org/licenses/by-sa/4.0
